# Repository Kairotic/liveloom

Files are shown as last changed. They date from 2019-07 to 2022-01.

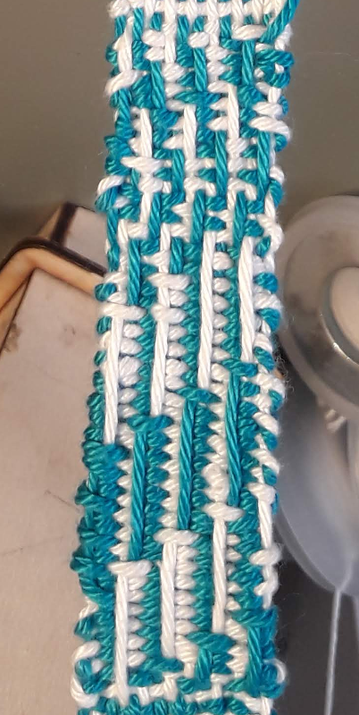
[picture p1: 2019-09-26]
paper/float-small.png

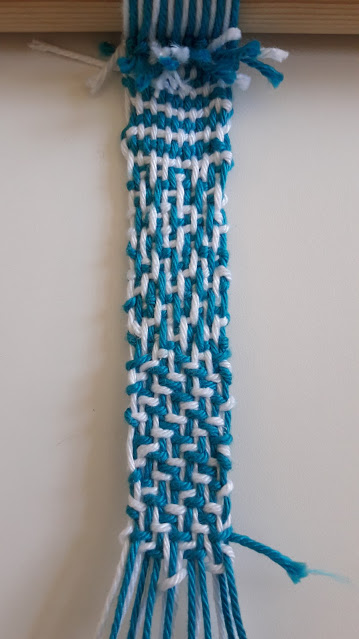
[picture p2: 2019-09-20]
paper/20190919_163823.jpg

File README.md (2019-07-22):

# Liveloom

A warp-weighted loom, live codeable via solenoids.

## lasercut.svg

This creates the shapes required to lasercut a loom from 3mm
material. I used baltic birch plywood, MDF would likely do just as
well.

## Other things needed

- 4mm diameter metal rod
- 25mm diameter wooden rod
- Solenoids - "DC 12V 10mm Push-Pull Actuator Frame Type Electromagnet
  Solenoid Electric Magnet" - can be found for about £2
  each. With this design, I recommend getting either 12 or 16.
- Relays - I used a board with 16 of them. "16-channel Relay Module
  Board 5v12v".
- Arduino (and 'jumper jerky' wire) to control the relays
- PSU for the relays
- PSU for the solenoids - This needs some power. I used "RS PRO 102W
  Embedded Switch Mode Power Supply SMPS, 8.5A, 12V dc". (You might
  need even more amps to power all your relays at once)
- Loom weights, one per thread - I recommend small plastic weighted
  kumihimo bobbins for this, then you can easily store the warp
  inside, but you can also use smallish bolts and wrap the warp around..
- Screws to attach the solenoids, I think I needed M2.5 screws for
  mine.
- wire to connect up the solenoids etc. This needs to be fairly heavy
  duty, to take the amps!
- diodes to protect everything against kickback from the
  solenoids. I still need to add these myself!

## Rough instructions

My plywood was bendier in one direction - basically if there is a
grain have it go horizontal otherwise E1/E2 will bend too much with
the weight of the solenoids.

A* and B* are the main legs and supports. D0 slots into the support
and is where I screw my relay switch board.

Below you see 'lollypop stick' heddles. Each has a 'mouth', two of the
things that look like capital As slot into each 'mouth', creating a
nice strike area for the solenoid. Half of the heddles have bends, so
the solenoids can be on two axes (doubling the number you can have in
a given amount of space).

The circles above the heddles are wooden washers to space the lollypop
sticks out so they line up with the solenoids, I woodglue one to each
heddle. These are then threaded onto a 4mm metal rod. I add a small
metal washer or two to line everything up with the solenoids.

E1 and E2 are what the solenoids are screwed on to.

C* are assembled with wood glue, and then slotted into the front of
the legs A4, with E1 and E2 and the 4mm rod slotted in using the
provided holes.

Contact alex@slab.org with any questions - I'd be happy offer advice
to get you up and running.

## WWL.hs

An experimental haskell library for live coding the loom.

Start ghci, and then initialise the library like this (replacing with the path to your arduino's USB connection):
```
:load WWL

(set, next, undo, again, show) <- startFs "/dev/serial/by-id/usb-Arduino__www.arduino.cc__0043_5573731323135141A191-if00"
```

Then code a structure like this:

```
set $ every 2 rev $ twill 1 $ cycle [up,down,down,up]
```

And run `next` to send the next line to the loom, `again` to send it again, or `undo` to go back.

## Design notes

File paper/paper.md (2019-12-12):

% The Live Loom

---
author: Alex McLean, Deutsches Museum
email: alex@slab.org
header-includes: |
    \usepackage{caption}
    \usepackage{subcaption}
	\usepackage{wrapfig}
...

# Abstract

This paper introduces the *Live Loom*, a warp-weighted hand-loom
augmented with computer control, using a visual live coding
environment. The traditional weaving technique of colour-and-weave
interference patterns are explored, revealing the digital,
computational nature of weaving that predates the invention of
discrete mathematics as it is commonly understood. Early results of
live coding such patterns, in the process of learning how to weave, is
shared.

# Introduction

*Live coding* is the exploratory practice of changing code while it
runs. A live coder uses a programming language as a live interface to
a running process, and therefore its inputs and outputs. This allows
the programmer to participate in the performing arts, for example to
create live coded music, video or dance. Live coding may be used to
refer to any use of code in any kind of live situation, but for the
purposes of this paper, we will focus on live coding as live
improvisation, where code is written without a fixed aim, often from a
notional 'blank slate'.

*Weaving* is a textile craft, where parallel threads known as the
*warp* are held under tension, allowing a second set of threads known
as the *weft* to be passed over and under the warp threads to create a
textile fabric. Different textile techniques produce different
results; for example in terms of structure, weaving and knitting have
very little in common with each other.

This paper investigates how live coding and weaving can be brought
together, looking for ways to ground the contemporary practice of live
coding in ancient craft. In the following I take a loosely
auto-ethnographic approach, introducing the Live Loom, and its use
both for understanding weaving and reflecting on the shared history of
live coding and textile practice that it might reveal.

# Background

Connections between textile craft and computation have been very well
explored in the digital arts and beyond. However, as David McCallum
notes, such work often does not engage with structure or long history
of textiles, but instead treats the three dimensional structure of
weave as a simple grid or raster [@mccallum_glitching_2018, \S
0.3.1]. McCallum's own work explores the notion of 'glitch' in media
art and how it transfers to textile structures, but given that the
latter has developed over a far longer period than the former, it is
not surprising that along the way he finds much that media art can
learn from textiles.

In the weaving industry, the technology of computer-controlled looms
is of course also well developed. In the present work we are
interested in analogies with live coding and 'hands on' computer
control. Such interaction is not afforded by most machine looms, where
the human weaver is replaced by a machine. However, hand-operated
computer controlled looms *do* exist, and the present work is much
inspired by experiments I conducted on the TC1 loom in Textiles
Zentrum Haslach, Austria [@mclean_fabricating_2018].

*Stitching Worlds* is a recent, far reaching project imagining a world
where textiles more overtly formed the basis of contemporary
electronic technology [@kurbak_stitching_2018]. Works produced from
this project include the "Embroidered Computer" with Irene Posch and
collaborators, a working 8-bit computer embroidered in gold. This work
integrates textile electro-mechanical relays into a fabric,
demonstrating that a feminist approach to linking textiles with
computing goes far beyond metaphor - textiles can compute.

## Feminist alternative history

Although not the primary focus of the present work, comparing the
contemporary practice of live coding with the ancient craft of
hand-weaving has potential to support and extend a somewhat obscured
feminist history of computation. Feminist perspectives on computing
and weaving are hardly new, a well-known reference point being Sadie
Plant's influential text "Zeros and Ones: Digital Women and the New
Technoculture" [@plant_zeros_1998]. However, the once dominant role of
women in computer programming has been steadily erased since the 1960s
and '70s [@hicks_programmed_2017], and despite recent efforts, gender
diversity in software engineering is an ongoing problem.

As a relatively new interdisciplinary practice that tries to reject
hierarchies^[See for example the Algorave Guidelines --
https://github.com/Algorave/guidelines], live coding offers an
opportunity to build a gender diverse culture, and this opportunity is
a core topic across live coding research and practice
[@armitage_spaces_2018]. Turkle and Papert related gender to the
plurality of relationships between coder and program observed in
children, describing a more conversational approach to coding, with
mid-course corrections rather than fixed-goals as *bricolage*
[@Turkle90, p. 136]. This approach is certainly evocative of live
coding, with the suggestion being that it is one likely to be favoured
by girls, but discouraged by instructors in favour of more fixed
design processes.

@armitage_spaces_2018 brings together female perspectives on live
coding in the Algorave scene, relating one interviewee's experience of
live coding "... as a way of working through their daily life, adding
structures to it and providing functions for being. These lived
patterns merge with their daydreams and expressions of colour and
geometry to form her live coded visuals." [@armitage_spaces_2018,
p. 39]. This again evokes Turkle and Papert's bricoleur, and indeed
the ancient social and intellectual function of weaving in building a
personal cosmos [@harlizius_kluck_ellen_2017_840005].

## Setting aside the Jacquard machine

The Jacquard machine is a well known device for individual control of
threads in the weaving process, classically through the use of punch
cards. From across computer science and popular culture, the Jacquard
machine is often invoked as part of an 'origin story' of computation,
following Charles Babbage's mention of it as an influence. However, the
Jacquard machine does not *do* computation, it is merely a mechanism
for accepting input data. The Jacquard machine therefore brings a
fundamental misunderstanding to the topic of weaving and computation
which is very difficult to work around.

Yes, weaving is computational, and yes, the Jacquard machine allowed
data to be fed into that computation. But the same computational
nature is present in all weaving, including traditions of hand weaving
developed over millennia [@harlizius_kluck_ellen_2017_3342554]. The
computation was already there before Jacquard, and by helping automate
the weaving process, his device only takes humans further away from
that computation. So while Jacquard's machine is often described in
terms of the beginning of the relationship between weaving and
computing, the opposite is true - it was an end.

So let's try to wipe the Jacquard machine from our minds in the
following discussion, not because the technology isn't interesting and
useful, but because the discussion around it is so full of
misunderstanding. Once we do that, we are able to see that such
machinery did not introduce any computation to weaving - the
computation was there already. As will become evident in this paper,
the computation is not in the machine, but in the weave.

# Introducing the Live Loom

Having set one mechanism aside, I introduce another. The Live Loom is
a warp-weighted loom, with solenoids attached so that warp threads may
be individually picked from software. First, I explain the technology
of the warp-weighted loom, and later explain the electro-mechanical
attachments on the Live Loom.

The primary purpose of any loom is to hold a group of parallel
threads, the *warp*, in parallel and under tension, allowing *weft*
threads to be woven over and under the warp threads. The warp-weighted
loom is an ancient technology, where tension comes from the effects of
gravity, by attaching weights to the bottom of the warp threads. By
contrast, on modern looms warp threads are generally horizontal, and
held in tension through mechanical means. The essential components of
a warp-weighted loom are therefore very simple, consisting of a frame
holding two horizontal bars in place, one to hang the warp from, and
another below separating alternate threads, keeping them in order, and
creating a potential gap (using weaving terminology, the *natural
shed*) for the weft to pass through by default. The simplicity of the
loom is also its advantage - the simpler the loom, the fewer
constraints and therefore more possibilities there are to weave
complex structures on it.

----

**FIGURE 1 AROUND HERE**

Note: For this figure, the following images to be arranged in a 3x3 grid:

plain-draft.png twill-draft.png satin-draft.png

plain-weave-a.png twill-weave-a.png satin-weave-a.png

plain-weave-b.png twill-weave-b.png satin-weave-b.png

**Caption** Figure 1: Fundamental weave structures, shown with binary 'draft' structure (top), simulated weave with light warp and dark weft (middle), and simulated weave with alternating light and dark warp and weft (bottom). These different structures lead to different physical properties and therefore uses (Emery, 2009).

\begin{figure}[!h]
\begin{subfigure}[t]{0.33\textwidth}
\includegraphics{plain-draft.png}
\end{subfigure}
\begin{subfigure}[t]{0.33\textwidth}
\includegraphics{twill-draft.png}
\end{subfigure}
\begin{subfigure}[t]{0.33\textwidth}
\includegraphics{satin-draft.png}
\end{subfigure}
\begin{subfigure}[t]{0.33\textwidth}
\includegraphics{plain-weave-a.png}
\end{subfigure}
\begin{subfigure}[t]{0.33\textwidth}
\includegraphics{twill-weave-a.png}
\end{subfigure}
\begin{subfigure}[t]{0.33\textwidth}
\includegraphics{satin-weave-a.png}
\end{subfigure}
\begin{subfigure}[t]{0.33\textwidth}
\includegraphics{plain-weave-b.png}
\end{subfigure}
\begin{subfigure}[t]{0.33\textwidth}
\includegraphics{twill-weave-b.png}
\end{subfigure}
\begin{subfigure}[t]{0.33\textwidth}
\includegraphics{satin-weave-b.png}
\end{subfigure}

\caption{\label{fundamental}Fundamental weave structures, shown with binary 'draft' structure (top), simulated weave with light warp and dark weft (middle), and simulated weave with alternating light and dark warp and weft (bottom). These different structures lead to different physical properties and therefore uses (Emery, 2009).}
\end{figure}

----

\flushleft

The weaving process involves a weft thread going over and under the
warp threads, following one of a very large range of possible
patterns, for example creating tabby, twill or satin structures
[@emery_primary_2009, see also Fig. 1]. Selective
warp threads are pulled forward, creating a new gap or shed between
the pulled and non-pulled warp threads, through which the weft travels
in a straight line. When the warp threads are returned, the weft is
trapped inside, and the next shed is prepared.

----

**FIGURE 2 GOES AROUND HERE**

Image: wwl.png

**Caption** Figure 2: The Live Loom, a warp-weighted loom, with live-codeable heddles via solenoid actuators.

\begin{figure}
\begin{center}
\includegraphics[width=0.48\textwidth]{wwl.png}
\end{center}
\caption{\label{liveloom}The Live Loom, a warp-weighted loom, with live-codeable heddles via solenoid actuators.}
\end{figure}

----

## Weaving technology

The Live Loom is shown in Figure 2. Although it carries a
contemporary 'maker' aesthetic due to its laser cut plywood
construction, at its core, it is a hand-loom following an ancient
warp-weighted loom design. The additional electro-mechanical parts do
not replace the core functions of the loom, but rather augment them in
order to allow threads to be selected using a computer language as
well as directly by hand. The hardware and software designs are
available as open hardware/free software
[@alex_mclean_kairotic/liveloom:_2019].

The Live Loom is fitted with a number of solenoids (currently
sixteen), mounted on two axes to double the number that could
otherwise fit in a given space. The solenoids are controlled by an
arduino micro-controller, via a bank of relays. When activated, each
solenoid will push against a stick, which pulls its corresponding warp
thread forward via a string. In this paper we refer to the wooden
stick and string collectively as the *heddle*. With each solenoid
controlling one warp thread, the resulting weave is currently
constrained to sixteen threads across.

Crucially, these solenoid movements are *not* designed to fully create
a shed. Instead this movement only 'offers up' warp threads to the
human weaver-coder, who then pulls the threads further by hand. This
seems like a deficiency of power and leverage, but is not; this
'offering up' means the weaver can choose whether or not to pull each
thread. This is particularly useful at the edges of the weave, where
adjustments are often required to produce a good fabric. 

The suggestive nature of instructions sent via the solenoids reminds
of the live coding choreographic work of @Sicchio14. We can think of
this process as not directly live coding a textile weave, but instead
suggesting bodily movements to produce the weave. When live coding
people rather than computers, it is humane to respect their ability to
exercise creativity and agency in the way they interpret instructions
given to them.

# Computing a weave

Before introducing a language for live coding the loom, lets first
look closer at the computational nature of weaving itself, focussing
on colour and weave effects. Such effects bring together different
dimensions or systems. Firstly, the structure of the weave - the
arrangement of ups and downs in the grid created by the meeting points
of warp and weft. Secondly, the colour patterning of warp and weft
threads. The visible colour at a particular point of the weave then
depends on two things - whether the warp or weft thread is visible
(i.e. whether the weft is under or over the warp) and what colour that
thread is. The result is an interference pattern between these two
systems, creating a deterministic, logical outcome that is nonetheless
very difficult for the layperson to predict.

As a simple example of this, consider the weave structure shown in
Fig. 3a, known as a draft pattern.  The black-and-white grid
shows the pattern of weft ups and downs represented as white and black
squares respectively. For example, the first row shows a weft thread
going under one warp, over two warps, and repeat. The second row shows
a weft thread going under two warps, over one warp, and then
repeating.

There are also coloured squares at the top and bottom, showing the
pattern of warp and weft thread colours respectively, in this case
both alternating between light green and dark blue. In order to find
what colour will be visible, we look at the weave structure. For black
squares, we know the warp colour is shown, so follow the column up to
find its colour, otherwise we follow the row to the left. ^[In
practice, there are other variables which change which colour thread
is visible, for example if weft threads are tightly packed, warp
threads are hidden completely.] From this we can see that where warp
and weft meet with a matching colour (in this case, every other cell
in a checkerboard pattern), the visible colour cannot be changed by
the structure. This is analogous to the Moire effect seen by placing
one net over another, with the visible result being the interference
of the upper and lower structures.

----

**FIGURE 3 AROUND HERE**

*Note: Three subfigures, arranged in a row:*

* draft.png, subcaption: a) Draft pattern
* draft-out.png, subcaption: b) Result
* weave-diagonal.jpg, subcaption: c) Actual result

**Caption** Figure 3: A draft pattern and the result of virtually and actually weaving it.

----

\flushleft

If we plot out the result of this interference between thread colour
and weave structure, we arrive at the image shown in Fig. 3b. This
result will be surprising to a layperson, not only is the vertical and
horizontal stripe of warp and weft not visible, but the diagonal runs
in a different direction to the underlying weave structure. This
experience will be familiar to those who have explored algorithmic
interference patterns in livecoding software such as TidalCycles or
Hydra, simple inputs often create unexpected, more complex results.

Finally, Fig. 3c shows a fabric woven using this
structure and alternating white and blue threads, created by a
workshop visitor on the Live Loom. The same features hold in the weave
itself, although are not too well defined, due to interaction between
the threads, and variation in density. The left and right edges are a
mess, because in practice such a structure simply cannot be woven at
the edges. Weft threads generally travel from left to right for one
row, and from right to left on the next. Therefore, if a weft ends a
row over a warp, and begins the next row also over a warp, then it
will not be woven at that point. A more experienced weaver would make
consistent changes at the edges (known as the *selvage*), such as
adding plain weave border, to ensure a coherent result.

The above description of colour and weave effects should give us pause
for thought. Weaving predates computer programming and indeed discrete
mathematics in general, but nonetheless is a discrete, logical and
therefore digital computational system. Furthermore, any hand-loom
affords exploration of this system. When considering the computational
nature of weaving then, we must be careful not to be dazzled by the
machinery or electronics of industrial and contemporary weaving
technology, when it is the ancient technology of the threads
themselves that provides the environment for computation.

# Coding the draft

We have already seen that weaving drafts are a form of code, which can
compute unexpected results when interpreted. Such weaving drafts are
themselves binary, digital images, developed well before electronic
digital computers. It is therefore straightforward to add a further
level of abstraction by using a programming language to create a
draft. The purpose of doing so is to create patterns from patterns,
making a rich space to explore weaving and gain tacit knowledge both
about how it works, and its relation to computation as it is more
conventionally understood in the context of programming
languages. Each such layer of abstraction takes us further away from
the material, but just as live coding of music brings together the
experience of coding and listening, the Live Loom brings together
coding with seeing and touching.

Figure 4a shows the current version of the Live Loom coding
interface. The code is shown on the left, using the visual live coding
interface Texture [@McLean11], originally designed as an exploratory
interface for the TidalCycles environment, but here re-purposed for a
system designed for discrete, binary draft patterns. The set of
available symbols and keywords are on the top right, which may be
dragged into the code using a mouse. On the bottom right a window into
the draft pattern is shown, with the row most recently being sent to
the Live Loom marked with blue squares on either side. Finally the row
number is written below, which in this case is higher than the number
of rows shown, as the previous rows have scrolled off the top. The
weaver-coder can manipulate the code with a mouse, while using arrow
keys on a keyboard to step forwards (or backwards) through the draft,
sending each warp lift to the loom to be actuated by the solenoids and
woven by the weaver.

Perhaps most notable is what is *not* shown in the software
interface. In particular, simulation of thread colour (such as that
shown in Fig 3) could easily be included, but is not, indeed thread
colour is not dealt with at all in the software, only on the
loom. Keeping colour on the loom takes focus away from any simulation
on screen and places it in the 'ground truth' of the material. After
all, colour is only one quality of thread, alongside thickness,
material, ply, tightness and direction of twist, tension and density
of warp and weft, and so on. Trying to simulate all of these
continuous variables on-screen would be an insurmountable task, and
focussing the software on the singular task of planning the discrete
structure of ups and downs works very well.

It is important to recognise that although the binary grid of a
weaving draft is contained in two dimensions, the structure it
describes is very much three dimensional. Indeed certain
two-dimensional patterns will result in more than one fabric, one on
top of the other, creating the possibilities of double weave
structures.^[ See https://penelope.hypotheses.org/1905 for Live Loom experimentation with double weave.]

## Live Loom language

The language currently used by the Live Loom is the pure functional
programming language *Haskell*, using its list datatype. Standard
Haskell lists are 'lazily evaluated', which means that infinitely long
lists can be represented and calculated on demand. A weave structure
is simply represented by a one dimensional list of Boolean values,
where *true* and *false* stands for *up* and *down* (or if you prefer,
*over* and *under*) respectively.

Listed in Table 1 below, the current number of functions for composing
draft patterns on the Live Loom is small but already provides a very
rich space of possibility. The weaver-coder begins with a list of ups
and downs, then applies functions to transform that list and/or
combine it with other lists.  The result is a language interface that
produces surprisingly complex results from simple elements.

| name | description |
|---|---|
| [] | An empty list |
| : | Adds a value to a list |
| up / down | Keywords representing the boolean values of up (over) and down (under) |
| cycle | Repeats a list forever |
| backforth | Reverses every other row |
| offset n | Offsets each row from the last, by the given number of threads |
| shift | Shifts each row by one thread |
| rev | Reverses each rows | 
| every n f | Selectively applies function f to every nth row |
| invert | Turns all ups to downs, and vice versa |
| zipAnd a b | Combines two lists, resulting in up when both lists have an up |
| zipOr a b | Combines two lists, resulting in up when one or both lists has an up |
| zipXOr a b | Combines two lists, resulting in up when only one list has an up |

Table: **Table 1:** The values, functions and operators available in the Live Loom code interface.

# Working at the Live Loom

Figure 4 shows the Live Loom software interface next to the woven
outcome. This starkly shows the perceptual gap between code, draft and
weave, with little visual correspondence despite the structures of the
draft being a logical outcome from the code, and the weave being that
of the draft. The code is represented as a branching tree, the visual
interface directly showing the branching normally represented by
parenthesis [@McLean11]. This particular code creates the draft
pattern shown, which perhaps has the appearance of vines growing up a
wall. When this structure interferes with the alternating colours of
warp and weft, the final result appears in the weave as (to my eyes)
legs leaping into the air (Fig. 4b).

----

**FIGURE 4 AROUND HERE**

*Note: Two subfigures, arranged in a row:*

* caroline-draft.png, subcaption: a) Code (left) and resulting draft structure (bottom right)
* caroline.png, subcaption: b) Resulting weave

**Caption** Figure 4: Live Loom software interface and the woven result

\begin{figure}[!h]

\begin{subfigure}[t]{0.692\textwidth}
\includegraphics{caroline-draft.png}
\caption{\label{caroline-draft}Code (left) and resulting draft structure (bottom right)}
\end{subfigure}
\begin{subfigure}[t]{0.308\textwidth}
\includegraphics{caroline.png}
\caption{\label{caroline-result}Resulting weave}
\end{subfigure}
\caption{Live Loom software interface and the woven result}
\end{figure}

----

It is humbling that this leap from draft to weave constitutes ancient
knowledge, demonstrating mathematical logic that predates our
conventional view of mathematics. This brings historical grounding to
the analogous logical leap from code to draft, shown alongside.

It is worth noting that adding an additional level of abstraction to
the drafting of weaves is not novel. Indeed, it is very common in
weaving for patterns of threads to be grouped into a number of shafts,
where weave structure is created by patterns for lifting these
shafts. The binary grids we consider in the present paper are in such
cases drawn down from a draft composed of of threadings (how the
threads are grouped into shafts) and treadlings (how the shafts are
lifted over time). In a sense, the live coding language introduced in
this paper provides a flexible, interactive alternative to lift plans.

## Music of the loom

The solenoids are not triggered at once but in sequence, to even out
the use of electrical power, with less needed to hold a solenoid than
to move it. The most time-efficient way to do this would be to trigger
the 'up' threads, pulling the warps one after the other, evenly spaced
in time. However I have found it much more useful to include 'down'
threads in the timing, so each row takes the same amount of time to
actuate, no matter how many warps are being pulled forward. This gives
a clear rhythm to each row, where the 'clunk' of a solenoid is heard
for an up, and a silent pause is heard for downs. This rhythm breathes
life into the weaving process, making it easier to orient myself in
the pattern and spot errors, as I compare the rhythm I hear with the
threads I see. It also brings rhythmic enjoyment to the repetitive nature
of weaving, compelling me forward into the next row.

The solenoids have a particular 'duty cycle', meaning that it is best
not to keep them activated for too long, otherwise they may
overheat. Once a solenoid is activated, the micro-controller holds it
in place, giving enough time for the weaver to place a hand on the
heddles and pull selected warp threads forward. Although born from a
technical need, these few seconds add an additional sense of regulated
timing to the process of weaving. However if the heddles are not
caught in time, the weaver-coder can repeat the lift with a quick
press of the up arrow key. The weaver can also unweave by stepping
backwards through the structure with the left arrow, removing rather
than adding the weft by hand, for each step.

# Live Coding

So far we have discussed action, but not live reaction. We have looked
at coding the loom with a draft, and coding the coding of the loom by
introducing a language for composing a draft, but we haven't discussed
live coding - the changing of code in response. Let's do that now.

## Changing patterns

Live coding of music is often characterised by comparatively slow,
continuous changes. Changes are heard immediately, but the complexity
of music grows with the code. The experience of the Live Loom is
rather different, where a small change tends to have a large, global
effect, but each change takes time to become apparent; rows are only
produced at a rate of a few per minute, and it might take two or three
repeats of a pattern before its nature can really be felt.  These
big differences from small edits are due to multiple levels of
interference, between code, draft and weave.

A change from one pattern to the next also presents a problem of
transition, where one pattern might not sit well with the next,
potentially creating a physically uneven structure, with undesirable
floats (see below). It can take a disturbed row or two before the
weave settles into the next structure. There are certainly parallels
here with live coding music and indeed music in general, where a
sudden change can be jarring, without a careful transition. Managing
this transition is probably best done at the loom, adjusting each shed
at the heddles by hand.

At this slow pace of change though, we are in the domain analogous to
slow coding rather than frenzy of an algorave. Where each decision has
long term consequences, there is a need for careful
consideration. Furthermore in weaving we work with physical thread,
rather than with the metaphorical thread of time as with live coding
of music. This means that we are able to undo a weave in a way that we
cannot undo music, and change our minds. By unweaving, the weaver,
like the mythological figure of Penelope, resists external forces.

## Embracing error

Live coders are known for embracing error, and so it is fortunate that
it is so easy to produce a draft which is unweavable. For example,
there is the problem of 'floats', lengths of unwoven fibre created
wherever there is a contiguous series of either ups or downs in the
warp or weft direction. Indeed, where there are only either ups or
downs in a given row or column, that thread will not be woven into the
fabric at all. In response to a problematic draft, the weaver can do
one of three things -- change the code to look for a more weavable
draft, ignore activated heddles or pull additional ones to change the
weave directly, or just attempt to weave the pattern anyway.

----

**FIGURE 5 AROUND HERE**

*Note: Two subfigures, side-by-side (same height, left hand one will be wider):*

a) doubleweft-code.png, caption: Live Loom code and draft showing pairs of identical rows.
b) doubleweft.jpg, caption: The resulting weave, showing pairs of wefts that have travelled through the same shed.

**Caption:** Figure 5

\begin{figure}[!h]

\begin{subfigure}[t]{0.6835\textwidth}
\includegraphics{doubleweft-code.png}
\caption{\label{doubleweft-code}Live Loom code and draft showing pairs of identical rows.}
\end{subfigure}
\begin{subfigure}[t]{0.3165\textwidth}
\includegraphics{doubleweft-small.jpg}
\caption{\label{doubleweft}The resulting weave, showing pairs of wefts that have
  travelled through the same shed.}
\end{subfigure}
\caption{}
\end{figure}

-----

In the draft shown in Figure 5a, the draft looked unweavable to my
naive eyes, due to the pairs of identical rows within it. Where this
happens, pairs of consecutive wefts are passed through the same
shed. I thought this would result in a mess, but out of curiosity went
ahead anyway to produce the weave shown in Fig. 5b. I
found that with care the wefts would still run parallel and stay in
order, largely maintaining the 'correct' structure
on-screen. Furthermore, because the repeat in the draft consists of an
odd number of rows, and I was weaving with two different wefts, the
wefts would alternate between either travelling through the same shed
from one side to the other together, or in opposite directions. By
embracing this 'error' I arrived at a (to me) surprising, pleasing,
and subtle result, although there are undoubtedly many such surprises
on the way to becoming an experienced weaver, and I have far to go.

## Weaving the edit

Decisions at the Live Loom are taken slowly, responding to problems
and opportunities as they arise in the weave. Figure 6a shows the
starting point for another improvised weave, a draft appearing to be a
kind of hatched vertical pattern, drifting downwards to the left, with
lines sometimes joining or breaking. When it came to weaving this
structure (see Fig. 7a), two features slowly became
apparent -- the pervasive pairs of ups and downs on the weft, offset
from one row to the next, seemed to result in the warp spreading out
vertically, and therefore partially hiding the warp at points where I
expected it to be visible. This created an a partly *weft-faced*
weave. However, some long floating threads were present on the warp
direction, and the weft-facing only accentuated the presence of these
long warps lying on top.

----

FIGURE 6 AROUND HERE

*Note: Six images, arranged in two rows of three, and labelled from a) to f)*

a) improv-a.png
b) improv-b.png
c) improv-c.png

d) improv-d.png
e) improv-e.png
f) improv-f.png

**Caption** Figure 6: Screenshots of Live Loom interface at six different points in the weaving of fabric (see Fig. 7)

\begin{figure}[!h]

\begin{subfigure}[t]{0.33\textwidth}
\includegraphics{improv-a.png}
\caption{}
\end{subfigure}
\begin{subfigure}[t]{0.33\textwidth}
\includegraphics{improv-b.png}
\caption{}
\end{subfigure}
\begin{subfigure}[t]{0.33\textwidth}
\includegraphics{improv-c.png}
\caption{}
\end{subfigure}
\begin{subfigure}[t]{0.33\textwidth}
\includegraphics{improv-d.png}
\caption{}
\end{subfigure}
\begin{subfigure}[t]{0.33\textwidth}
\includegraphics{improv-e.png}
\caption{}
\end{subfigure}
\begin{subfigure}[t]{0.33\textwidth}
\includegraphics{improv-f.png}
\caption{}
\end{subfigure}

\caption{\label{screenshots}Screenshots of Live Loom interface at six different points in the weaving of fabric (see Fig. \ref{float-result}).}
\end{figure}

----

After weaving 20 rows of this pattern (Fig. 7a), I hit a snag - the
pattern of repeating warp floats drifted until they sat at both edges
of the fabric, seen in Fig. 6b. I realised that having floats at the
selvage would cause the textile to lose its otherwise uniform width,
and I decided I neither wanted this effect or to change it by hand; I
had been enjoying working the two wefts together at the selvage, and
felt that having a warp float there would create a mess. So instead I
changed the structure to that seen in 6c, adding code to invert every
other row, as an effort to break up warp floats. However, after a few
rows of weaving the edit (Fig. 7b) to the point in the interface shown
in Fig. 6d, I realised that by breaking up some floats, I had only
created new ones. Another tweak shown in Fig. 6e, this time changing a
number from 3 to 1, seemed to fix it. However once I started weaving I
realised the floats were still there, but now so long that they took
up the whole edge and so were no longer visible on-screen!

----

**FIGURE 7 GOES AROUND HERE**

float.pdf

**Caption** Figure 7: Result of improvised weave edits shown in Figure 6.

----

This time I decided having such long floats was an interesting enough
challenge to pursue, and embraced this compounded error as an
opportunity to experiment more with creating extra binding points at
the selvage by hand. I continued with this structure for 53 rows, up
until the point seen in Fig. 6f.  The resulting weave shown in 7c did
indeed turn out to be interesting, the resulting weave curiously
appearing to be much more coherent than the draft pattern. As the long
floating warp threads stepped one warp to the left, they cycled
between white and blue, over a steep diagonal. This time, the
resulting motif reminded me of Quipu knots.

The resulting experimental weave we have seen in Fig. 7 charts an
experiment in three stages. First, the initial serendipitous discovery
of a) a weft-faced structure with warp floats. Then transition b) as I
searched for a solution to a perceived problem at the selvage. Finally
a longer section c), with some manual experimentation at the
selvage. The resulting fabric tells a story of its making, from a
starting point, to prevarication and decision, with further learning
points charted along the edge as I learned to deal with the selvage.

# Conclusion

This paper has explored how the principles of live coding may apply to
the warp-weighted loom. However, in connecting a live coding pattern
language to the practice of weaving, we find that weaving is already
abundant with computational patterns, and in particular that
historical drafting techniques already demonstrate a similar
computational abstraction from the resulting woven textile, as code
does from media in the live coded performing arts. Nonetheless by
adding another layer of abstraction to that which has been present in
weaving since ancient times, and using solenoids in communicating
movement from the code to the weaver, the Live Loom allows creative
exploration of woven patterns in a way that is sympathetic to the
repetitive, yet cognitive nature of hand-weaving.

There is much to follow the preliminary work introduced here. This
paper has purposefully focussed on understanding of weave from the
perspective of live coding, taking care to have respect for this
technological craft that has developed since Ancient times. It could
be however that weaving practice could benefit from such a computer
language interface, for example replacing the current relatively
time-consuming process of uploading bitmap images whenever the pattern
is changed on a TC2 loom. Introducing 'real' trained weavers to the
Live Loom would undoubtedly also turn up valuable criticism of its
design. Furthermore while some hands-on workshops have already been
conducted, more involved long-form work with workshop participants are
needed to explore the possibilities of the loom in helping people
explore the complexities and possibilities of hand-weaving.

# Acknowledgements

This research is conducted by the PENELOPE project, with funding from the European Research Council (ERC) under the Horizon 2020 research and innovation programme of the European Union, grant agreement No 682711.

# References

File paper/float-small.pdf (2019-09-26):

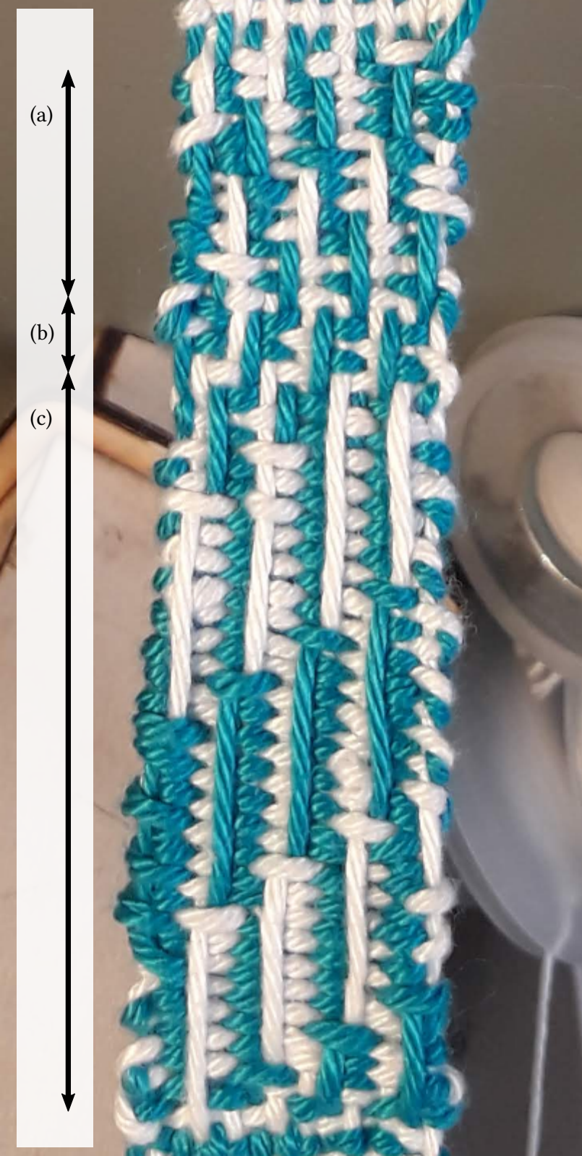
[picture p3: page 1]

(a)

(b)

(c)

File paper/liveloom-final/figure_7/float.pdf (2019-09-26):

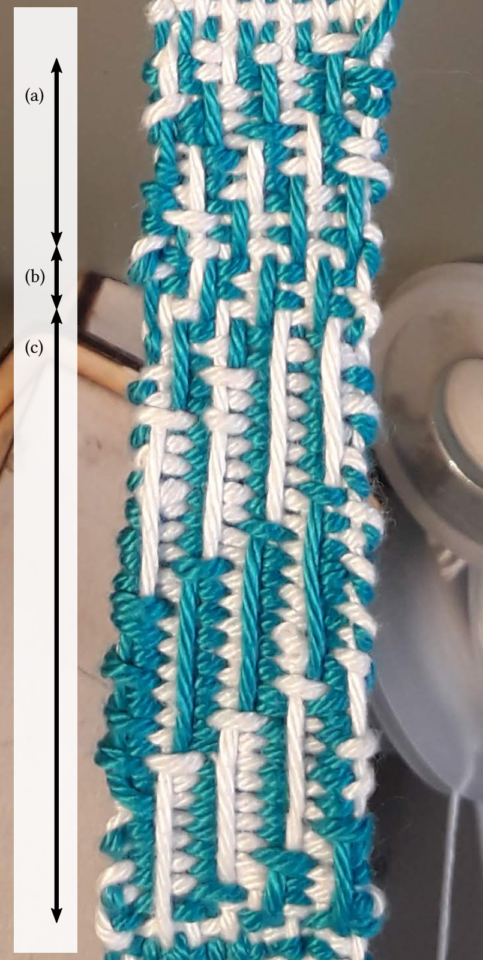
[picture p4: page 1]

(a)

(b)

(c)

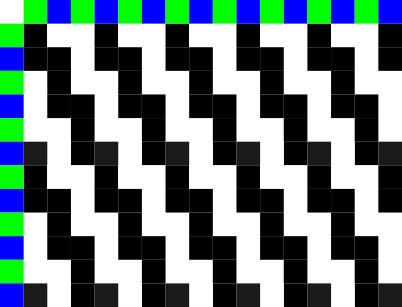
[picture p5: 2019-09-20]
paper/liveloom-final/figure_3/draft.png

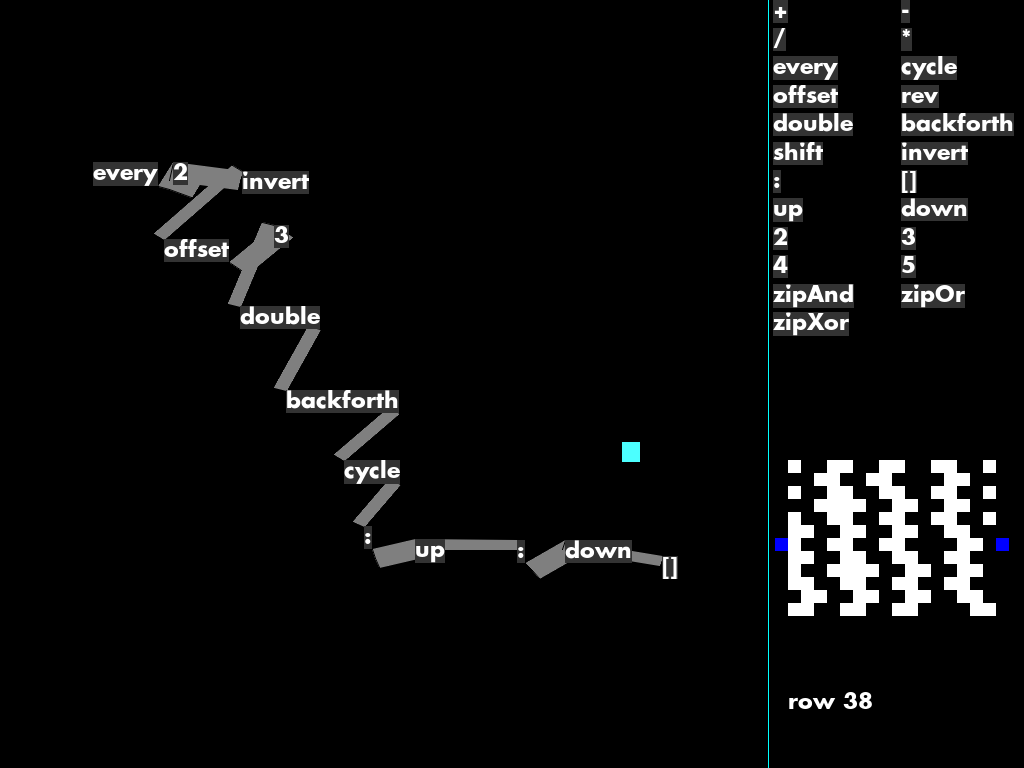
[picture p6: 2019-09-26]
paper/liveloom-final/figure_6/improv-d.png

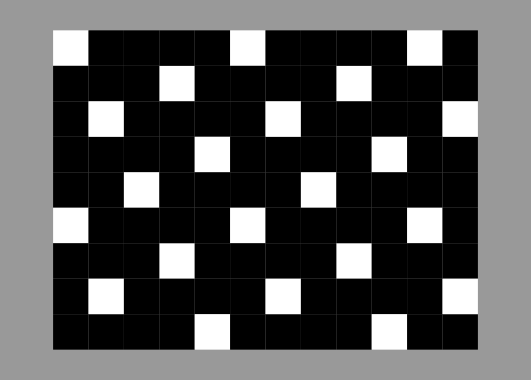
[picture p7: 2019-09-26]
paper/liveloom-final/figure_1/satin-draft.png

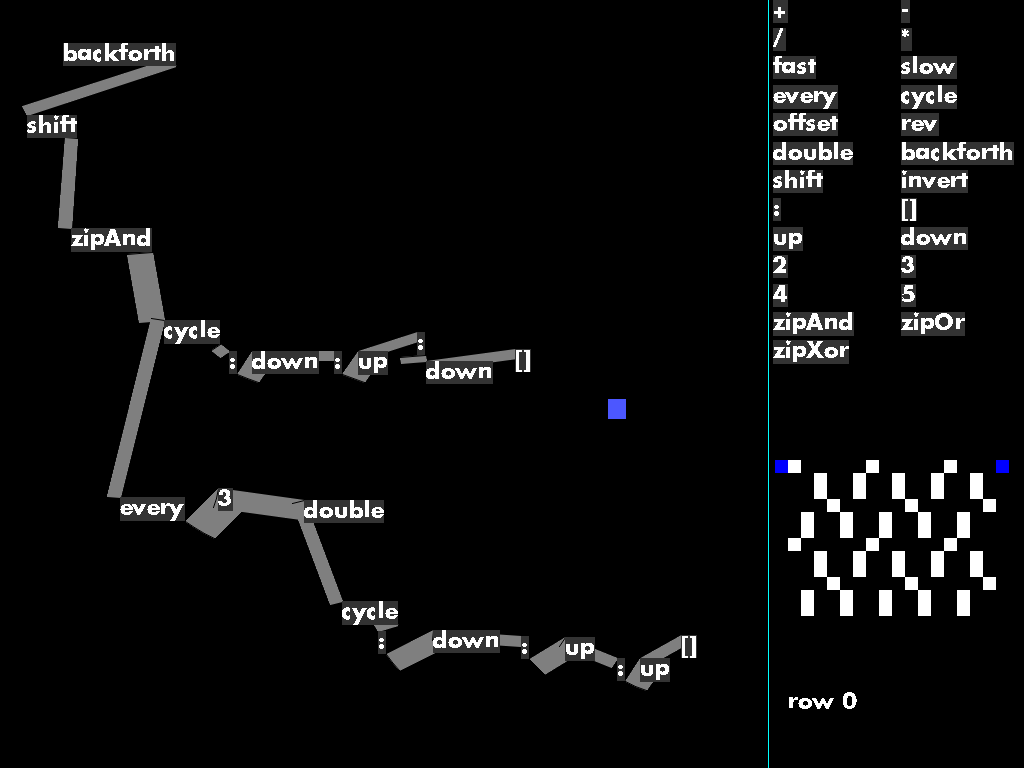
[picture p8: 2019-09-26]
paper/liveloom-final/figure_5/doubleweft-code.png

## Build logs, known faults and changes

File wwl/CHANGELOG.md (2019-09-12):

# Revision history for wwl

## 0.1.0.0 -- YYYY-mm-dd

* First version. Released on an unsuspecting world.

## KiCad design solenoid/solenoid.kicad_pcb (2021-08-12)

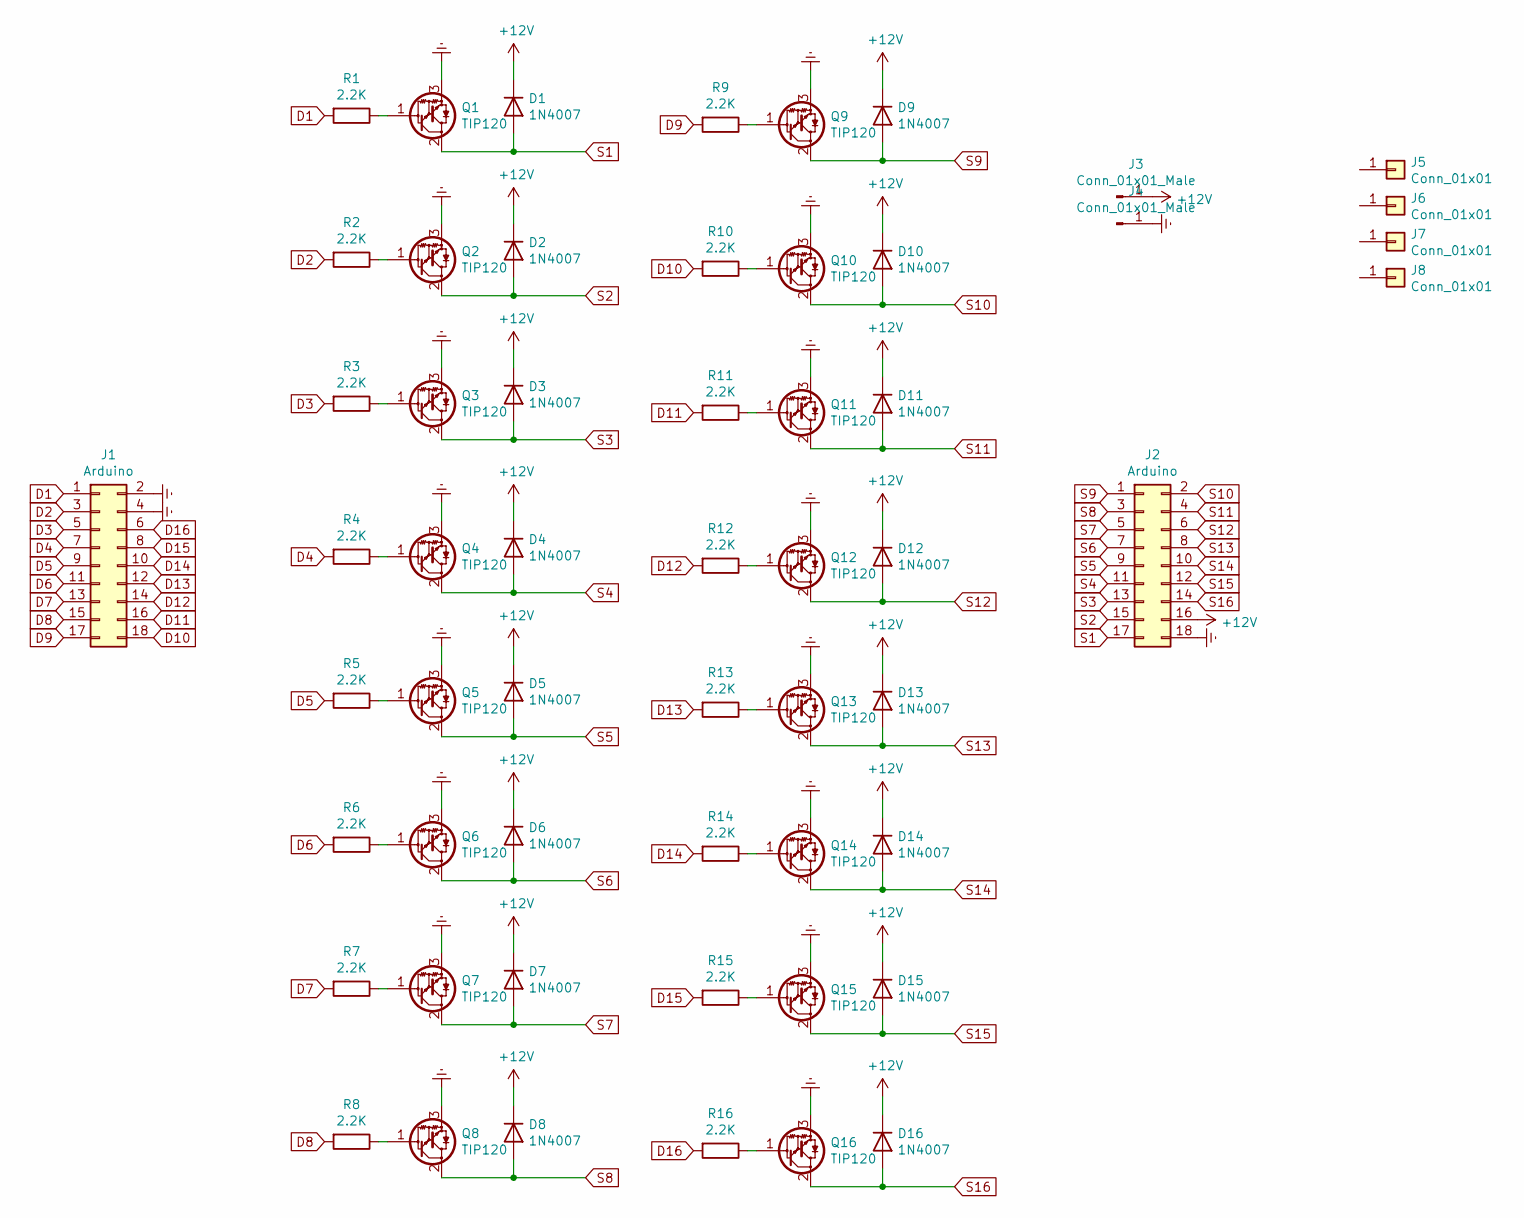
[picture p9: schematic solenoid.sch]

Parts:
D1, D2, D3, D4, D5, D6, D7, D8, D9, D10, D11, D12, D13, D14, D15, D16: 1N4007; D_DO-41_SOD81_P10.16mm_Horizontal
J1, J2: Arduino; PinHeader_2x09_P2.54mm_Vertical
J3, J4: Conn_01x01_Male; Pin_D1.0mm_L10.0mm
J5, J6, J7, J8: Conn_01x01; MountingHole_2.2mm_M2_Pad_Via
Q1, Q2, Q3, Q4, Q5, Q6, Q7, Q8, Q9, Q10, Q11, Q12, Q13, Q14, Q15, Q16: TIP120; TO-220-3_Vertical
R1, R2, R3, R4, R5, R6, R7, R8, R9, R10, R11, R12, R13, R14, R15, R16: 2.2K; R_Axial_DIN0309_L9.0mm_D3.2mm_P12.70mm_Horizontal

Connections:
+12V: D1.1 (K), D2.1 (K), D3.1 (K), D4.1 (K), D5.1 (K), D6.1 (K), D7.1 (K), D8.1 (K), D9.1 (K), D10.1 (K), D11.1 (K), D12.1 (K), D13.1 (K), D14.1 (K), D15.1 (K), D16.1 (K), J2.16, J3.1
D1: J1.1, R1.2
D2: J1.3, R2.2
D3: J1.5, R3.2
D4: J1.7, R4.2
D5: J1.9, R5.2
D6: J1.11, R6.2
D7: J1.13, R7.2
D8: J1.15, R8.2
D9: J1.17, R9.2
D10: J1.18, R10.2
D11: J1.16, R11.2
D12: J1.14, R12.2
D13: J1.12, R13.2
D14: J1.10, R14.2
D15: J1.8, R15.2
D16: J1.6, R16.2
Earth: J1.2, J1.4, J2.18, J4.1, Q1.3 (E), Q2.3 (E), Q3.3 (E), Q4.3 (E), Q5.3 (E), Q6.3 (E), Q7.3 (E), Q8.3 (E), Q9.3 (E), Q10.3 (E), Q11.3 (E), Q12.3 (E), Q13.3 (E), Q14.3 (E), Q15.3 (E), Q16.3 (E)
unnamed: Q1.1 (B), R1.1
unnamed: Q2.1 (B), R2.1
unnamed: Q3.1 (B), R3.1
unnamed: Q4.1 (B), R4.1
unnamed: Q5.1 (B), R5.1
unnamed: Q6.1 (B), R6.1
unnamed: Q7.1 (B), R7.1
unnamed: Q8.1 (B), R8.1
unnamed: Q9.1 (B), R9.1
unnamed: Q10.1 (B), R10.1
unnamed: Q11.1 (B), R11.1
unnamed: Q12.1 (B), R12.1
unnamed: Q13.1 (B), R13.1
unnamed: Q14.1 (B), R14.1
unnamed: Q15.1 (B), R15.1
unnamed: Q16.1 (B), R16.1
S1: D1.2 (A), J2.17, Q1.2 (C)
S2: D2.2 (A), J2.15, Q2.2 (C)
S3: D3.2 (A), J2.13, Q3.2 (C)
S4: D4.2 (A), J2.11, Q4.2 (C)
S5: D5.2 (A), J2.9, Q5.2 (C)
S6: D6.2 (A), J2.7, Q6.2 (C)
S7: D7.2 (A), J2.5, Q7.2 (C)
S8: D8.2 (A), J2.3, Q8.2 (C)
S9: D9.2 (A), J2.1, Q9.2 (C)
S10: D10.2 (A), J2.2, Q10.2 (C)
S11: D11.2 (A), J2.4, Q11.2 (C)
S12: D12.2 (A), J2.6, Q12.2 (C)
S13: D13.2 (A), J2.8, Q13.2 (C)
S14: D14.2 (A), J2.10, Q14.2 (C)
S15: D15.2 (A), J2.12, Q15.2 (C)
S16: D16.2 (A), J2.14, Q16.2 (C)

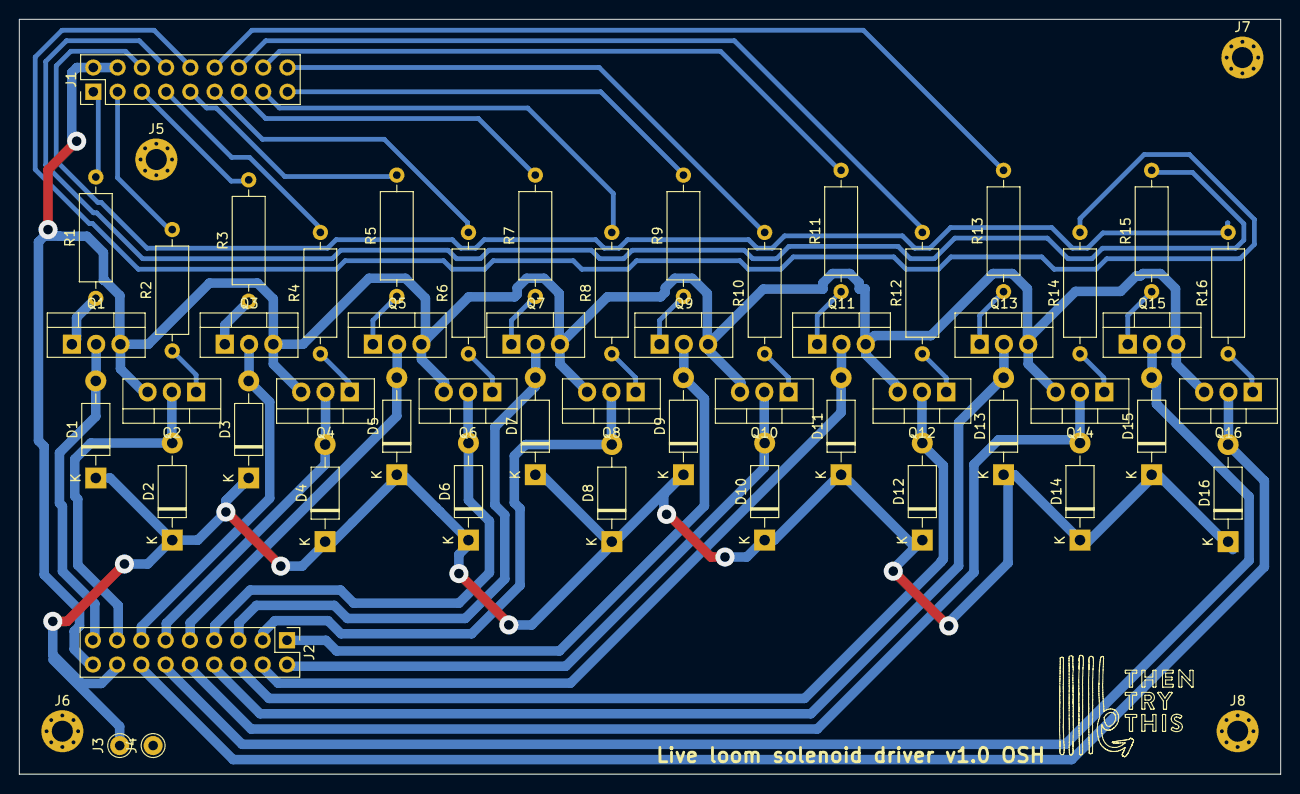
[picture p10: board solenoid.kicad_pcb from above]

Board: 2 copper layers, 132.0 x 79.0 mm, 56 parts (0 on the bottom side), 50 nets.

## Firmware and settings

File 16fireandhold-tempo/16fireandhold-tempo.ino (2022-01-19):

/*
 * Arduino code to control 16 channel relay with Arduino UNO
 * 
 * Written by Ahmad Shamshiri for Robojax.com on Sunday Oct 08, 2018 
 * at 10:35 in Ajax, Ontario, Canada
 * Watch video instruction for this code: https://youtu.be/Q9aBI4ELKC4
 * 
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
    You should have received a copy of the GNU General Public License
    along with this program.  If not, see <https://www.gnu.org/licenses/>.
 */

// weave 1
//const int=-\\\\\\\ controlPin[16] = {6,10,A1,11,5,9,A2,12,4,8,A3,A0,3,7,2,13}; // define pins
// weave 2
//const int controlPin[16] = {8,A4,9,A3,6,A1,7,A2,4,12,5,A0,2,10,3,11}; // define pins
//const int controlPin[16] = {11,3,12,4,A0,5,13,6,A1,7,A2,8,A3,9,2,10};
// weave 3
const int controlPin[16] = {2,3,4,5,6,7,8,9,10,11,13,A0,A1,A2,A3,A4}; // define pins

int external_tempo = false;
int debug = false;


void setup() {
  for(int i=0; i<16; i++)
  {
    pinMode(controlPin[i], OUTPUT);// set pin as output
    digitalWrite(controlPin[i], LOW); 
  }
  
  Serial.begin(115200);// initialize serial monitor with 115200 baud
  Serial.print("hello\n");
}

int maxBits = 16;
int incoming[16] = {0,0,0,0,0,0,0,0,0,0,0,0,0,0,0,0};
int active[16] = {0,0,0,0,0,0,0,0,0,0,0,0,0,0,0,0};
int incoming_n = 0;
int weakness = 2;
double tempo = (110.0/60.0*2)/1000.0;
unsigned long first_tick_time = millis();
int tick = 0;
int updated_tick = 0;
int hold_ticks = 16;
int t = 0;

void update_pattern() {
  for (int i=0; i<maxBits; ++i) {
    active[i] = incoming[i];
    incoming[i] = 0;
  }
  incoming_n = 0;
  // todo - modulo this to sync with measure?
  updated_tick = tick;
}

int update_tick() {
  if (!external_tempo) {
    unsigned long since = millis() - first_tick_time;
    // calculate from start time - avoids compounding floating point errors
    int now_tick = floor(((double)since) * tempo);
    if (now_tick > tick) {
      tick = now_tick;
    }
  }
  return(tick);
}

void pulse_solenoids() {
  static int pulses = 0;
  int pulsed[16] = {0,0,0,0,0,0,0,0,0,0,0,0,0,0,0,0};
  
  int last_tick = update_tick();
  while (update_tick() == last_tick) {
    delay(1); // is this needed?
  }
  //Serial.write("aha\n");
  last_tick = update_tick();

  for (int i=0; i < (maxBits + 12); ++i) {
    long int d = 0;
    int pulse = 0;
    while (update_tick() == last_tick) {
      for (int j=0; j < maxBits; ++j) {
        int on = ((j == i) || ((j < i) && ((pulse % weakness) == (j % weakness)))) && active[j];
        digitalWrite(controlPin[j], on ? HIGH : LOW);
      } 
      pulse++;
    }
    last_tick = update_tick();
  }
  
  for (int j=0; j < maxBits; ++j) {
    digitalWrite(controlPin[j], LOW);
  } 
  

  /*
  if (debug) {
    char msg[256];
    sprintf(msg, "tick %d - %d %d %d %d %d %d %d %d %d %d %d %d %d %d %d %d\n",tick, 
            pulsed[0], pulsed[1], pulsed[2], pulsed[3], 
            pulsed[4], pulsed[5], pulsed[6], pulsed[7], 
            pulsed[8], pulsed[9], pulsed[10], pulsed[11], 
            pulsed[12], pulsed[13], pulsed[14], pulsed[15]
           );
    Serial.write(msg);
  }
  */

}

void loop() {
  int c;

  while(Serial.available()) {
    c = Serial.read();
    if ((c == '0' || c == '1') && incoming_n < maxBits) {
      incoming[incoming_n] = c == '1';
      incoming_n++;
    }
    else {
      if (c=='x') {
        update_pattern();
        pulse_solenoids();

      }
      else if (c=='t' && external_tempo) {
        tick++;
      }
    }
  }
}

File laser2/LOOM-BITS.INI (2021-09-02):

[Technics_Laser_Data]
ModifyTechCFG=0
LayersNumber=2
ExportRows=1
ExportColumns=1
ExportRowSpace=0.00000
ExportColumnSpace=0.00000
ExportRowCW=0.00000
ExportColumnCW=0.00000
LogicOrgPositionX=560.03582
LogicOrgPositionY=344.19975
LogicOrgPositionZ=-9999999.00000
AtOnceExport=1
IsTwoLaserWorking=0
TableZeroPositionX=0.00000
TableZeroPositionY=0.00000
OutputTimes=1
DelayTime=0
FeedLength=0.00000
FeedSpeed=5.00000
FeedDelayTime=0
MinX=89.96418
MaxX=560.03582
MinY=55.80025
MaxY=344.19975
ChangeSerialNo=0
ArrayMinX=89.96418
ArrayMaxX=560.03582
ArrayMinY=55.80025
ArrayMaxY=344.19975
LayerColor_0=16776960
LayerColor_1=65280
ClipBoxPower=40.00000
ClipBoxPower2=40.00000
ClipBoxOffsetLen=2.00000
ClipBoxSpeed=25.00000
AlignMachineZPos=0.00000
RouteLength=0.00000
RoutePointNumber=0
OffsetLaserPower=0.00000
OffsetWorkSpeedPer=1.00000
ZHeightForLaserFocus=0.00000
OneWorkNeedTimes=1
TotalWorkTimes=0
[CoordSystem_0]
LogicOrgPosition1=560.03582
LogicOrgPosition2=344.19975
LogicOrgPosition3=-9999999.00000
SPLITBLOCK_NUMBER=2
SPLITBLOCK_NUMBER_0=0.00000
SPLITBLOCK_NUMBER_1=100000.00000
[CreateTechnicsCodeMgr]
PrjHasModifyCFG=1
[TechnicsLayers_16776960]
TechnicsMode=TECHNICS_LASERCUT
LaserCutConnerPower=17.00000
LaserCutWorkPower=45.00000
LaserCutConnerPower2=85.00000
LaserCutWorkPower2=90.00000
LaserCutFrequency=20000
LaserCutOptimizePathType=1
LaserCutInnerToOuter=1
LaserCutInnerToOuter2=0
LaserCutDownToUpper=0
LaserCutBlockHeight=150.00000
LaserCutAutoSetPathDir=0
LaserCutCicleMinSegNumber=36
LaserCutDisperseLength=0.02000
LaserCutCloseGapLength=0.00000
LaserCutOverlapLength=0.00000
LaserCutAdjustForClose=0
LaserCutQXEnterLength=0.00000
LaserCutDelayMoveTime=0.00000
LaserCutOpenGZDelayTime=0.00000
LaserCutOpenLaserDelayTime=0.00000
LaserCutCloseLaserDelayTime=0.00000
LaserCutDelayTimeAfterCloseLaser=0.00000
LaserCutOneAxisBackLashLength=0.00000
LaserCutTwoAxisBackLashLength=0.00000
LaserCutBackLashAddSpaceLength=8.00000
LaserCutBlowGasType=2
LaserCutAheadBlowGasTimes=0.00000
LaserCutNoCloseGasTimes=0.00000
LaserCutSpeed=20.00000
LaserCutGWAcc=80.00000
LaserCutGWTime=0.01000
LaserCutTrackSize=100
LaserCutLineLength=0.00000
SpaceCutLineLength=0.00000
bSpaceLineFirst=0
LaserCutAdjustMove=0
LaserCutAdjustMoveDelay=0.00000
LaserCutUpLen=0.00000
LaserCutCircleSpeedNum=0
TechnicsWorkTimes=2
GROUP_ROWS_0=1
GROUP_COLUMNS_0=1
GROUP_ROWSPACE_0=0.00000
GROUP_COLUMNSPACE_0=0.00000
GROUP_ROWCWSPACE_0=0.00000
GROUP_COLUMNCWSPACE_0=0.00000
GROUP_MINX_0=126.06423
GROUP_MAXX_0=550.09633
GROUP_MINY_0=59.80041
GROUP_MAXY_0=337.82793
[TechnicsLayers_65280]
TechnicsMode=TECHNICS_LASERCUT
LaserCutConnerPower=17.00000
LaserCutWorkPower=45.00000
LaserCutConnerPower2=85.00000
LaserCutWorkPower2=90.00000
LaserCutFrequency=20000
LaserCutOptimizePathType=1
LaserCutInnerToOuter=1
LaserCutInnerToOuter2=0
LaserCutDownToUpper=0
LaserCutBlockHeight=150.00000
LaserCutAutoSetPathDir=0
LaserCutCicleMinSegNumber=36
LaserCutDisperseLength=0.02000
LaserCutCloseGapLength=0.00000
LaserCutOverlapLength=0.00000
LaserCutAdjustForClose=0
LaserCutQXEnterLength=0.00000
LaserCutDelayMoveTime=0.00000
LaserCutOpenGZDelayTime=0.00000
LaserCutOpenLaserDelayTime=0.00000
LaserCutCloseLaserDelayTime=0.00000
LaserCutDelayTimeAfterCloseLaser=0.00000
LaserCutOneAxisBackLashLength=0.00000
LaserCutTwoAxisBackLashLength=0.00000
LaserCutBackLashAddSpaceLength=8.00000
LaserCutBlowGasType=2
LaserCutAheadBlowGasTimes=0.00000
LaserCutNoCloseGasTimes=0.00000
LaserCutSpeed=20.00000
LaserCutGWAcc=80.00000
LaserCutGWTime=0.01000
LaserCutTrackSize=100
LaserCutLineLength=0.00000
SpaceCutLineLength=0.00000
bSpaceLineFirst=0
LaserCutAdjustMove=0
LaserCutAdjustMoveDelay=0.00000
LaserCutUpLen=0.00000
LaserCutCircleSpeedNum=0
TechnicsWorkTimes=2
GROUP_ROWS_0=1
GROUP_COLUMNS_0=1
GROUP_ROWSPACE_0=0.00000
GROUP_COLUMNSPACE_0=0.00000
GROUP_ROWCWSPACE_0=0.00000
GROUP_COLUMNCWSPACE_0=0.00000
GROUP_MINX_0=89.96418
GROUP_MAXX_0=560.03582
GROUP_MINY_0=55.80025
GROUP_MAXY_0=344.19975
[TechnicsLayers_0]
TechnicsMode=TECHNICS_LASERCUT
LaserCutConnerPower=17.00000
LaserCutWorkPower=60.00000
LaserCutConnerPower2=85.00000
LaserCutWorkPower2=90.00000
LaserCutFrequency=20000
LaserCutOptimizePathType=1
LaserCutInnerToOuter=1
LaserCutInnerToOuter2=0
LaserCutDownToUpper=0
LaserCutBlockHeight=150.00000
LaserCutAutoSetPathDir=0
LaserCutCicleMinSegNumber=36
LaserCutDisperseLength=0.02000
LaserCutCloseGapLength=0.00000
LaserCutOverlapLength=0.00000
LaserCutAdjustForClose=0
LaserCutQXEnterLength=0.00000
LaserCutDelayMoveTime=0.00000
LaserCutOpenGZDelayTime=0.00000
LaserCutOpenLaserDelayTime=0.00000
LaserCutCloseLaserDelayTime=0.00000
LaserCutDelayTimeAfterCloseLaser=0.00000
LaserCutOneAxisBackLashLength=0.00000
LaserCutTwoAxisBackLashLength=0.00000
LaserCutBackLashAddSpaceLength=8.00000
LaserCutBlowGasType=2
LaserCutAheadBlowGasTimes=0.00000
LaserCutNoCloseGasTimes=0.00000
LaserCutSpeed=20.00000
LaserCutGWAcc=80.00000
LaserCutGWTime=0.01000
LaserCutTrackSize=100
LaserCutLineLength=0.00000
SpaceCutLineLength=0.00000
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

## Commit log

2021-04-27 added solenoid kicad files and gerber/cnc gcode
    [solenoid.kicad_pcb, solenoid.sch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]
2021-07-22 mass production version updates
    [solenoid.kicad_pcb, solenoid.sch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]
2022-01-19 Try to implement twill (not working yet)
    [weave.py]

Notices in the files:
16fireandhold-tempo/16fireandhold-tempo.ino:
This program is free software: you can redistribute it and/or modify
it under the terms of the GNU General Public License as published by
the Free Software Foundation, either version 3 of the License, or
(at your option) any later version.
